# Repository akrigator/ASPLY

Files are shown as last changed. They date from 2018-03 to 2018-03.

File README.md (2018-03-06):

ASPLY
=====

Control block for  the 'Kronasteel Gala 600 inox' kitche hood based on atmega8/48/88/168/328 microcontroller

#Functions:
1. Manage light;
2. Manage 3 speed fan;
3. Adjustable timers for light and fan.

#Timer activation:
1. Hold one of channel button (light or fan speeds)  about 2,5 second till LED indicator starts blink (0.5 sec in turn on and 0.5 sec in turn off state);
2. Count 3 blinks of indicator to set timer for 30 minutes (each blink = 10 minutes);
3. Release the button - the channel function is activated, indicator blinks with low intencive (1 sec in turn on and 1 sec in turn off state) till timer is stopped;
4. Timer can be disabled by clicking same button again;

#Power cord pinout:
1. grey
2. brown
3. black - fan 3
4. blue - fan 2
5. red - fan 1
6. white - light

#Usefull link:
1. https://github.com/MCUdude/MiniCore - supporting of atmega 8/48/88/168 for ArduinoIDE;
2. https://github.com/dxinteractive/AnalogMultiButton - the library of buttons states and debouner for Arduino IDE.

#Flash atmega48:
1. Burn 'Arduino as ISP' sketch;
2. Pin Arduino board to atmega48 board on a breadboard;
3. Set Tools -> Programmer -> Arduino as ISP;
4. Set Tools -> Board -> Atmega48;
5. Set Tools -> Clock -> 8MHz internal;
6. Flash controller by Sketch -> Upload Using Programmer.

#Trouble shooting
If clear atmega48/88 is used and it works too slowly, you need to set correct fuse:

```
avrdude -c avrisp -p m48p -P /dev/cu.usbmodem1411 -b 19200 -U lfuse:w:0xE2:m -v
```

#Thanks for help
Виктор ! Михалин <vik-lab@mail.ru>

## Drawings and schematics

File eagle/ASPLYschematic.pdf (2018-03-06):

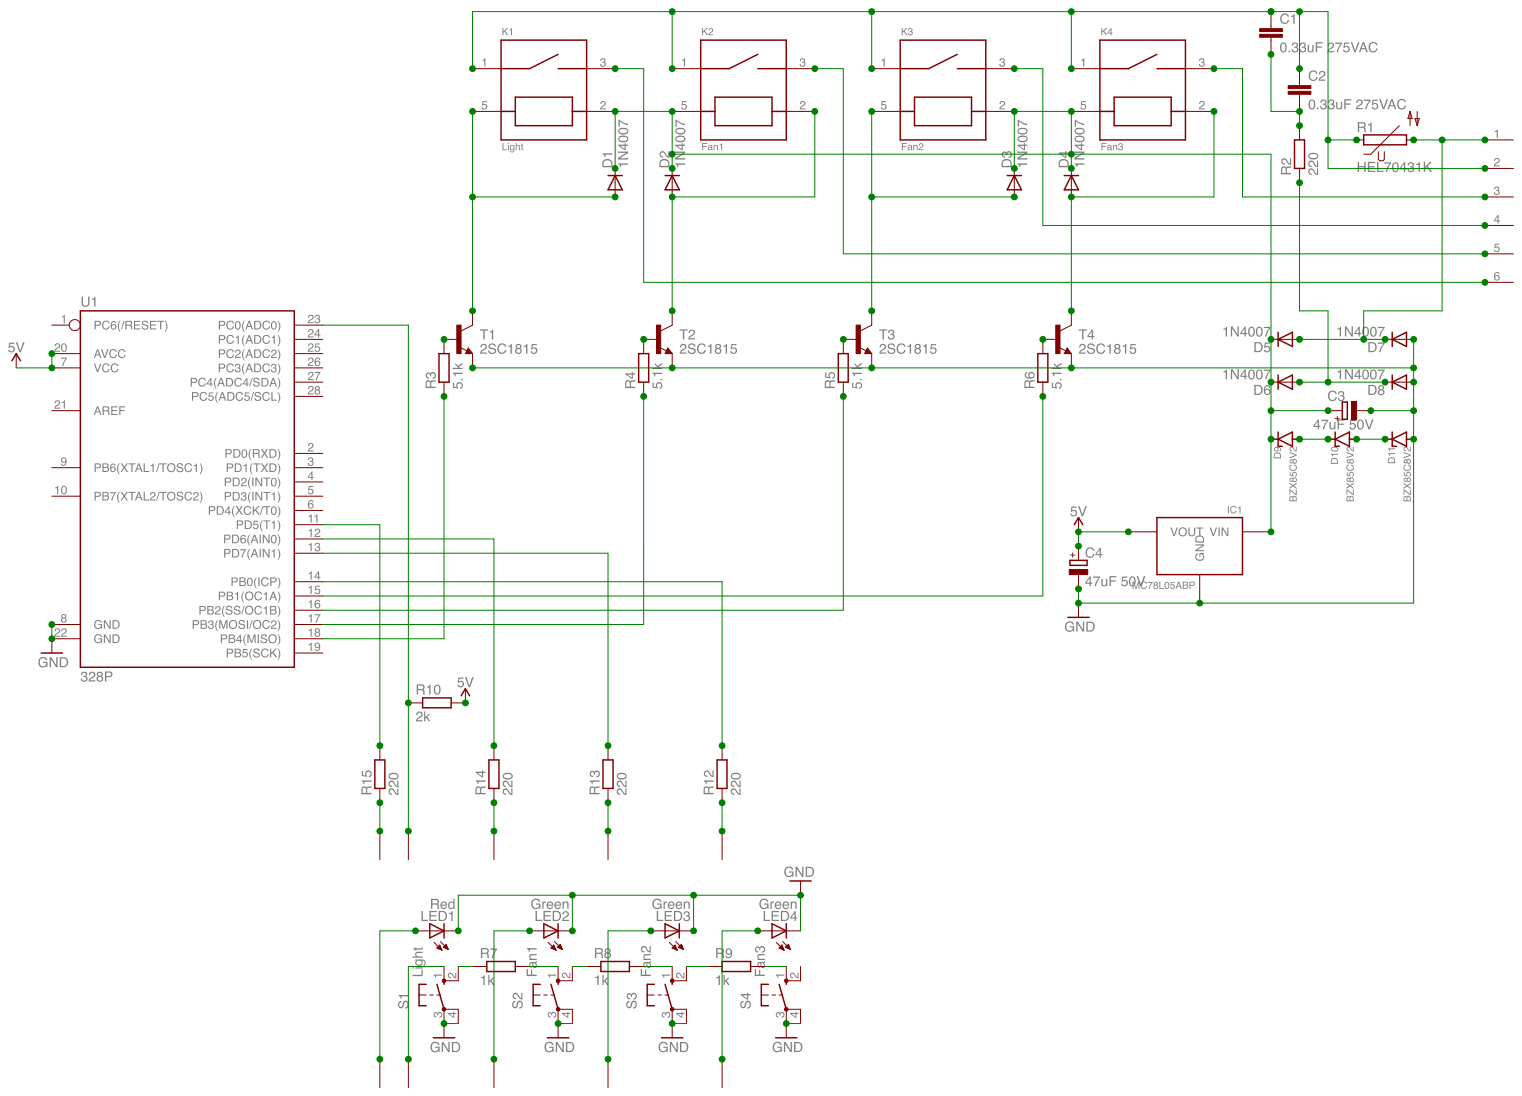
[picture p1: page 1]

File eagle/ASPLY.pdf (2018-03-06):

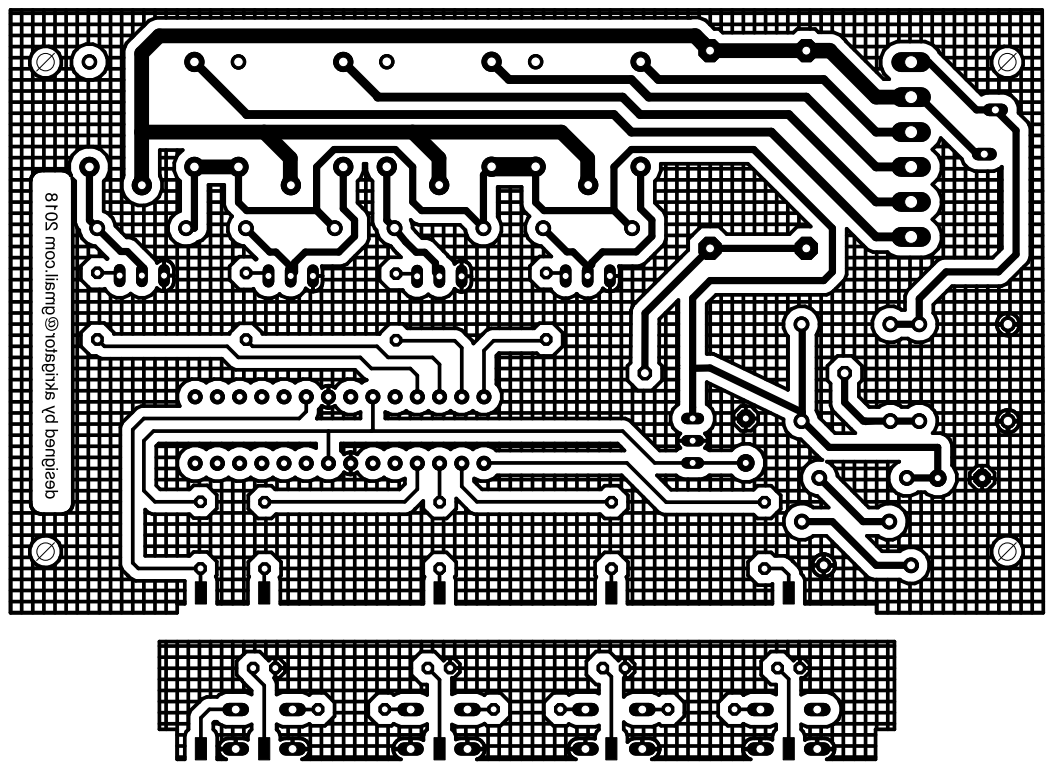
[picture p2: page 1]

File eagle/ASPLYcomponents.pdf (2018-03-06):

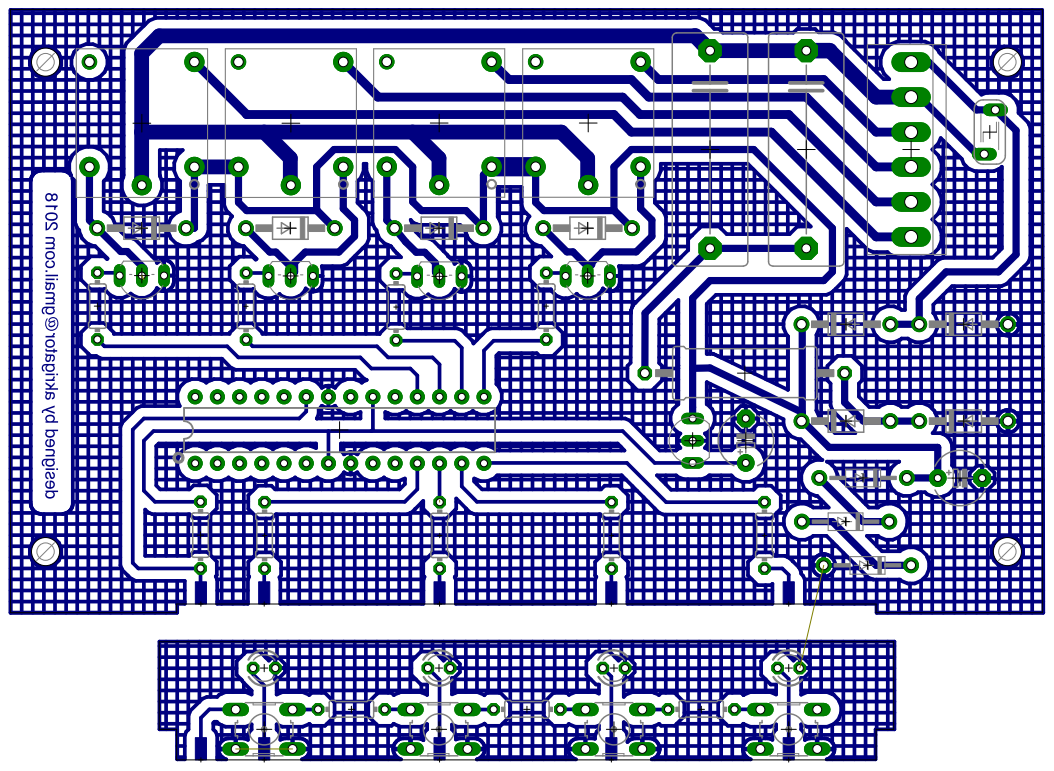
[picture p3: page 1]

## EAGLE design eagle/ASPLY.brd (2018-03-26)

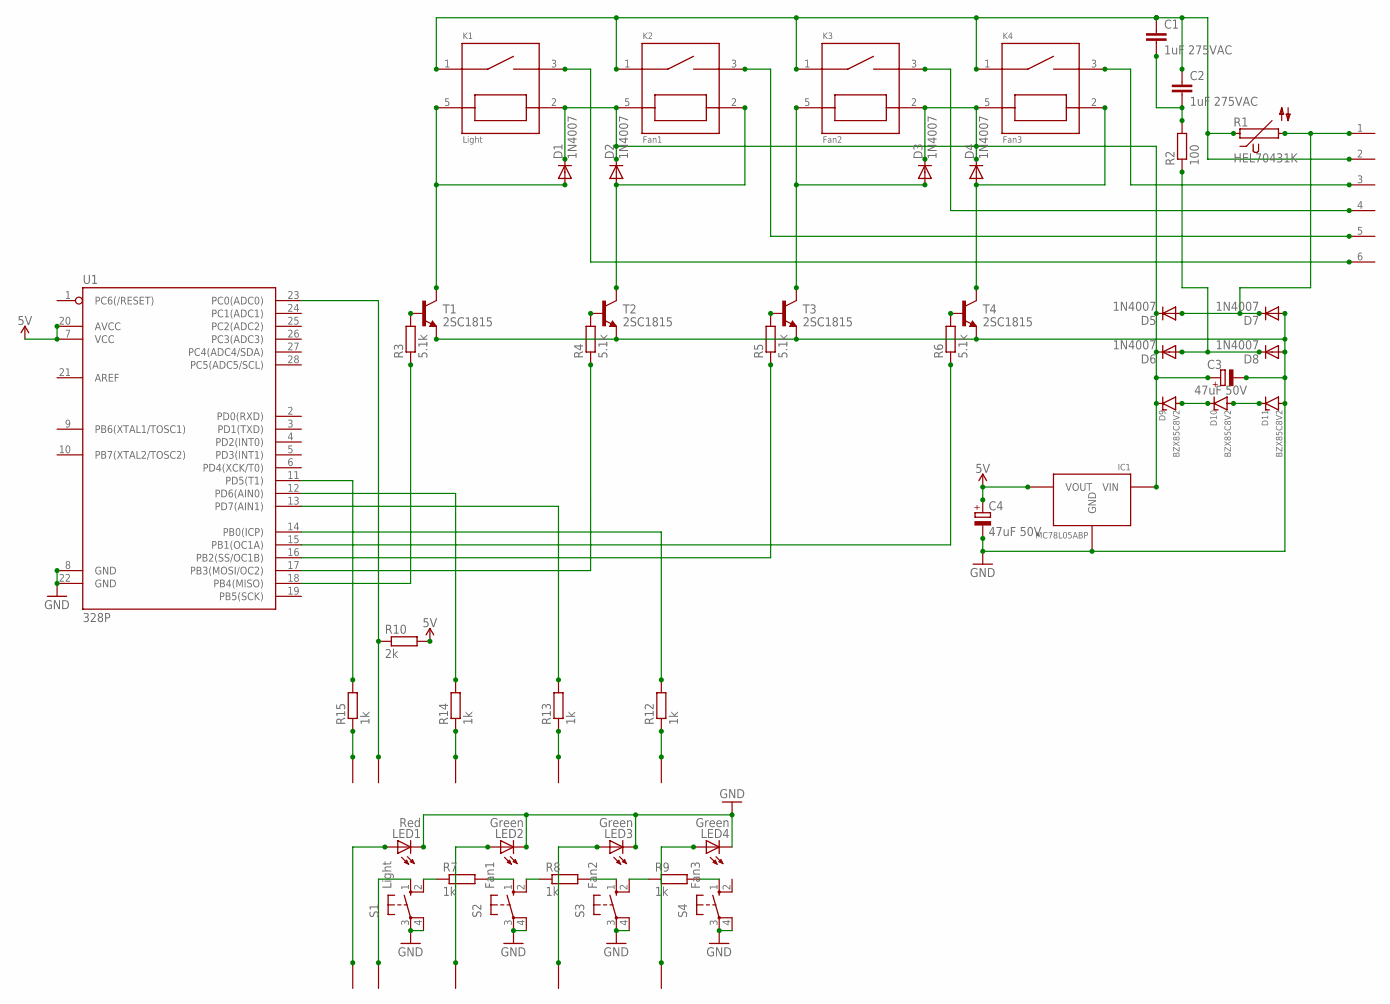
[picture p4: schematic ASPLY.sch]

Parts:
C1, C2: 1uF 275VAC; C22.5B8
C3, C4: 47uF 50V; E5-6
D1, D2, D3, D4, D5, D6, D7, D8: 1N4007; DO41-10
D9, D10, D11: BZX85C8V2; STAB
IC1: MC78L05ABP; TO-92
K1: Light; RELAY
K2: Fan1; RELAY
K3: Fan2; RELAY
K4: Fan3; RELAY
LED1: Red; LED3MM
LED2, LED3, LED4: Green; LED3MM
P1: MOLEX
R1: HEL70431K; S05K11
R2: 100; 0617/22
R3, R4, R5, R6: 5.1k; 0204/7
R7, R8, R9, R12, R13, R14, R15: 1k; 0204/7
R10: 2k; 0204/7
S1: Light; B3F-10XX
S2: Fan1; B3F-10XX
S3: Fan2; B3F-10XX
S4: Fan3; B3F-10XX
T1, T2, T3, T4: 2SC1815; TO92-ECB
U1: 328P; DIP28
U$1, U$3, U$5, U$7, U$8, U$13, U$14, U$16, U$18, U$20: PIN

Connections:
0: D5.A, D7.C, P1.1, R1.2
5V: C4.+, IC1.P$1 (VOUT), R10.2, U1.7 (VCC), U1.20 (AVCC)
24V: C3.+, D1.C, D2.C, D3.C, D4.C, D5.C, D6.C, D9.P$1, IC1.P$3 (VIN), K1.2, K2.5, K3.2, K4.5
220V: C1.1, C2.1, K1.1, K2.1, K3.1, K4.1, P1.2, R1.1
BUTTONS_INPUT: R10.1, U1.23 (PC0(ADC0)), U$8.P$1
GND: C3.-, C4.-, D7.A, D8.A, D11.P$2, IC1.P$2 (GND), LED1.K (C), LED2.K (C), LED3.K (C), LED4.K (C), S1.3, S1.4 (P1), S2.3, S2.4 (P1), S3.3, S3.4 (P1), S4.3, S4.4 (P1), T1.E, T2.E, T3.E, T4.E, U1.8 (GND), U1.22 (GND)
LED_FAN1: LED2.A, U$18.P$1
LED_FAN1_OUTPUT: R14.2, U1.12 (PD6(AIN0))
LED_FAN2: LED3.A, U$16.P$1
LED_FAN2_OUTPUT: R13.2, U1.13 (PD7(AIN1))
LED_FAN3: LED4.A, U$14.P$1
LED_FAN3_OUTPUT: R12.2, U1.14 (PB0(ICP))
LED_LIGHT: LED1.A, U$20.P$1
LED_LIGHT_OUTPUT: R15.2, U1.11 (PD5(T1))
unnamed: S1.1 (S), U$13.P$1
unnamed: K4.3, P1.3
unnamed: K3.3, P1.4
unnamed: K2.3, P1.5
unnamed: K1.3, P1.6
unnamed: R7.1, S1.2 (S1)
unnamed: R6.1, U1.15 (PB1(OC1A))
unnamed: R5.1, U1.16 (PB2(SS/OC1B))
unnamed: D1.A, K1.5, T1.C
unnamed: D2.A, K2.2, T2.C
unnamed: D3.A, K3.5, T3.C
unnamed: D4.A, K4.2, T4.C
unnamed: D6.A, D8.C, R2.1
unnamed: C1.2, C2.2, R2.2
unnamed: R7.2, S2.1 (S)
unnamed: D9.P$2, D10.P$1
unnamed: D10.P$2, D11.P$1
unnamed: R3.2, T1.B
unnamed: R4.2, T2.B
unnamed: R5.2, T3.B
unnamed: R6.2, T4.B
unnamed: R8.1, S2.2 (S1)
unnamed: R8.2, S3.1 (S)
unnamed: R9.1, S3.2 (S1)
unnamed: R9.2, S4.1 (S)
unnamed: R15.1, U$1.P$1
unnamed: R14.1, U$3.P$1
unnamed: R13.1, U$5.P$1
unnamed: R12.1, U$7.P$1
unnamed: R4.1, U1.17 (PB3(MOSI/OC2))
unnamed: R3.1, U1.18 (PB4(MISO))

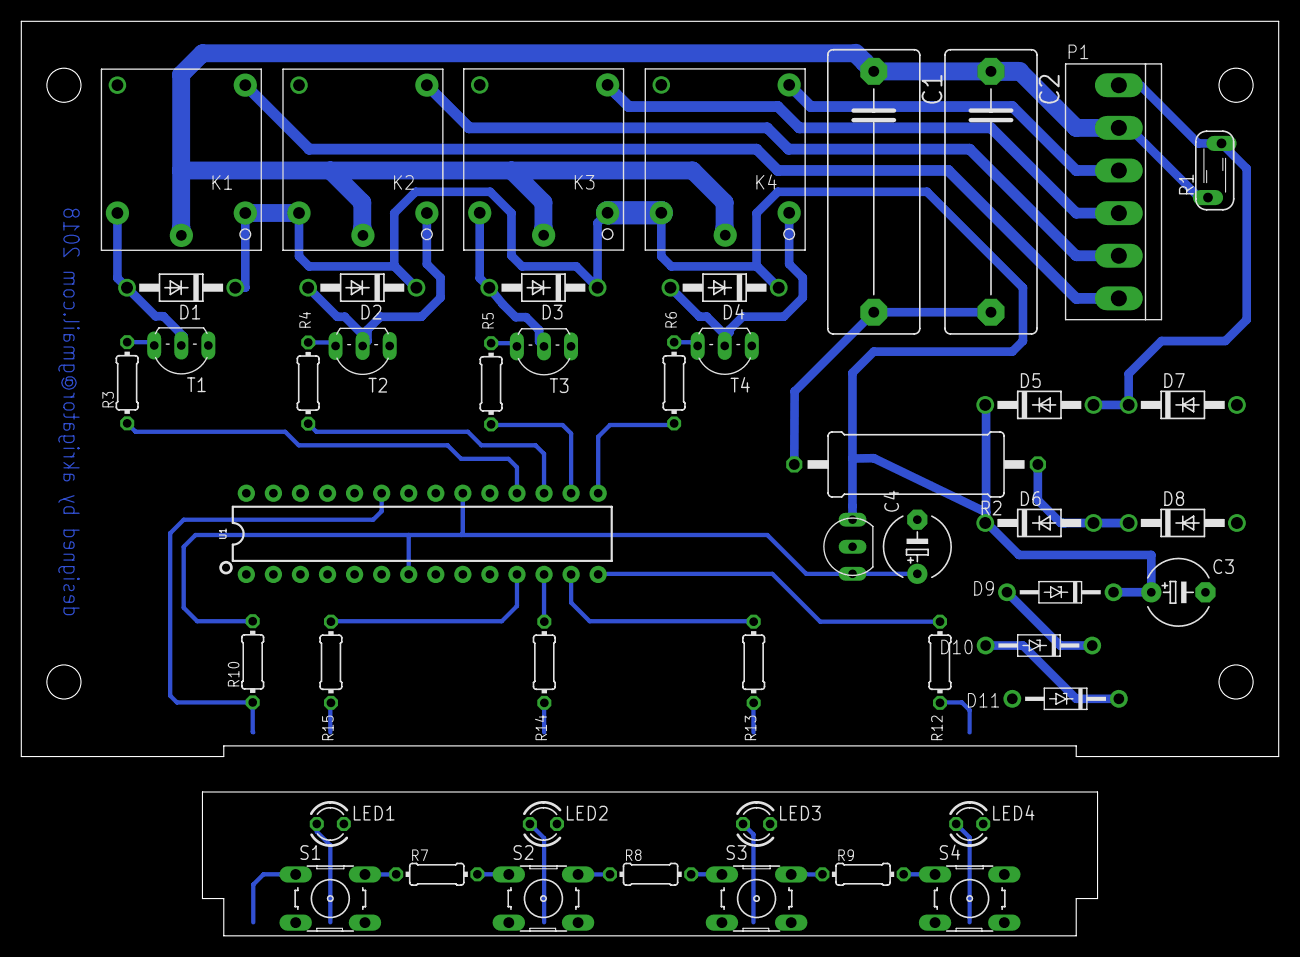
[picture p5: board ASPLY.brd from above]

Board: 1 copper layer, 118.0 x 85.8 mm, 58 parts (0 on the bottom side), 45 nets.

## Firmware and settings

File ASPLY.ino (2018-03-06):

#include <AnalogMultiButton.h>

#define BUTTONS_PIN A0
#define LED_LIGHT   5
#define LED_FAN1    6
#define LED_FAN2    7
#define LED_FAN3    8
#define CTRL_LIGHT  9
#define CTRL_FAN1   10
#define CTRL_FAN2   11
#define CTRL_FAN3   12

#define TIMER_ACTIVATION_DELAY 2500
#define TIMER_ACTIVATION_BLINK 500
#define TIMER_BLINK            1000
#define TIMER_BASE             600000

enum Channels {CHANNEL_LIGHT, CHANNEL_FAN1, CHANNEL_FAN2, CHANNEL_FAN3, CHANNELS_TOTAL};
const int BUTTONS_VALUES[CHANNELS_TOTAL] = {40, 343, 511, 613};

AnalogMultiButton buttons(BUTTONS_PIN, CHANNELS_TOTAL, BUTTONS_VALUES);

struct Output {
  const byte pin;
  unsigned long blink_timer;
  unsigned int blink_count;
  byte state;
  Output(byte pinv): pin(pinv), state(LOW), blink_timer(0), blink_count(0) {};
  void toggle(byte n_state) {state = n_state; digitalWrite(pin, state);};
  void on() {toggle(HIGH);};
  void off() {toggle(LOW); blink_count = 0;};
  void toggle() {toggle(state ? LOW : HIGH);};
  unsigned int blinking(unsigned long period) {
    unsigned long currentMillis = millis();
    if (currentMillis - blink_timer >= period) {
      blink_timer = currentMillis;
      toggle();
      blink_count++;
    }
    return blink_count/2;
  };
};

enum ChannelState {OFF, ON, TIMER_ACTIVATION, TIMER};

struct Channel {
  Output indicator;
  Output control;
  ChannelState state;
  unsigned long timer;
  unsigned int timer_multiply;
  
  Channel(byte led, byte ctrl): indicator(Output(led)), control(Output(ctrl)), state(OFF), timer(0) {
    pinMode(led, OUTPUT);
    pinMode(ctrl, OUTPUT);
  };
  void turnOn() {
    state = ON;
    indicator.on();
    control.on();
  };
  void turnOff() {
    state = OFF;
    indicator.off();
    control.off();
  };
  void timerActivation() {state = TIMER_ACTIVATION; indicator.blinking(TIMER_ACTIVATION_BLINK);};
  void startTimer() {state = TIMER; timer_multiply = indicator.blinking(TIMER_BLINK); control.on(); timer = millis();};
  void toggle() {
    if (state == OFF)
      turnOn();
    else 
      turnOff();
  };
  void tick() {
    unsigned long currentMillis = millis();
    if (timer > 0 && currentMillis - timer >= (timer_multiply * TIMER_BASE)) {
      timer = 0;
      turnOff();
    }
  };
  void update() {if (state > ON) {indicator.blinking(TIMER_BLINK); tick();}};
};

struct {
  Channel channels [CHANNELS_TOTAL] = {
    Channel(LED_LIGHT, CTRL_LIGHT),
    Channel(LED_FAN1, CTRL_FAN1),
    Channel(LED_FAN2, CTRL_FAN2),
    Channel(LED_FAN3, CTRL_FAN3)
  };
  void turnOffFans(byte j) {
    if (j != CHANNEL_LIGHT) {
      for (byte i = CHANNEL_FAN1; i < CHANNELS_TOTAL; i++) if (j != i) channels[i].turnOff();
    }
  };
} asply;

void setup() {}

void loop() {
  buttons.update();
  
  for (byte i = 0; i < CHANNELS_TOTAL; i++) {

    if (buttons.isPressed(i)) {
      if (buttons.isPressedAfter(i, TIMER_ACTIVATION_DELAY))
        asply.channels[i].timerActivation();
      else
        asply.channels[i].indicator.on();
    }

    if (buttons.onReleaseAfter(i, TIMER_ACTIVATION_DELAY)) {
      if (asply.channels[i].state != TIMER) {
        asply.turnOffFans(i);
        asply.channels[i].startTimer();
      }
    } else if (buttons.onRelease(i)) {
      asply.turnOffFans(i);
      asply.channels[i].toggle();
    }
    
    asply.channels[i].update();
  }

  delay(10);
}

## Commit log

2014-03-16 Ready to production
    ASPLY.ino с помощью Arduino Uno заливается на attiny45, плата
    изготавливается ЛУТом (ASPLY.pdf)
    [ASPLY.brd, ASPLY.sch]
2014-06-01 fix schema
    The connection of emitter and collector are fixed. Increase in current
    limiting resistors of transistors from 2 to 10 kOm
    [ASPLY.brd]
2014-06-07 voltage debounce
2018-03-04 New FW revision:
    - Add timers per each channels;
    - Timer depends on the switch holding time (count of indictor blnks * 10
    minutes).
2018-03-04 New HW revision:
    - Split LED and transistor manage
    [ASPLY.brd, ASPLY.sch]
2018-03-26 Setup power supply
    [ASPLY.brd, ASPLY.sch]

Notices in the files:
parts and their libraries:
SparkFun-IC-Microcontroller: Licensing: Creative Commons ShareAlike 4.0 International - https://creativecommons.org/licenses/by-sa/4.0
